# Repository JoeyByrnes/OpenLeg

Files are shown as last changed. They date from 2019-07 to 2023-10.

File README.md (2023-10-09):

<p align="center">
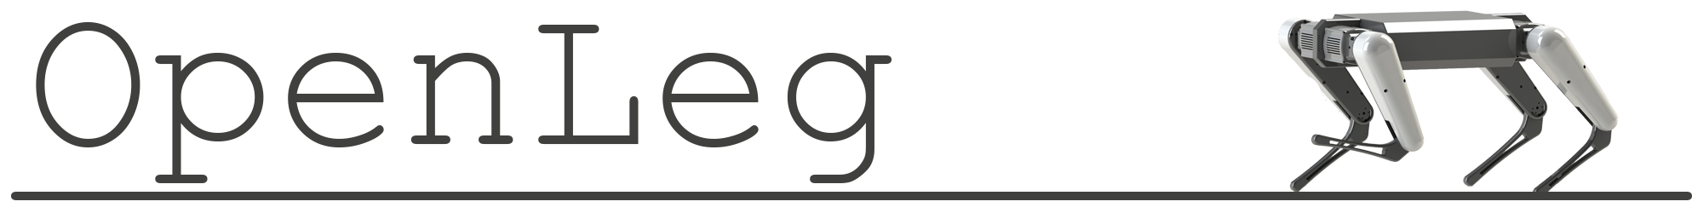
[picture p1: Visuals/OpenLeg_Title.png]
  
</p>

OpenLeg started as my Senior Design project for ECE445 at UIUC. The goal of the project is to provide a fully open source robotic leg capable of fast dynamic movements for research and development of quadrupedal robots. OpenLeg is intended to make development of robotic legs and associated algorithms accessible to hobbyists and researchers with tight schedules or budgets. 

All files required for replicating OpenLeg V1 are provided along with an assembly guide. All crucial mechanical and electrical assembly is now documented in the assembly guide. 

Feel free to reach out to me at openlegproject@gmail.com if you are interested in building the leg or contributing to the project.

Please keep in mind- OpenLeg isn't a finished product, it's still very much under development. You can expect everything in the assembly guide to be ready to use but for things not listed in the guide you should expect that there is still development needed to be done.

You can find the OpenLeg V1 Senior Design demo video here: https://www.youtube.com/watch?v=aXOSeKpADnk

Access the Full SolidWorks souce files for OpenLeg V1 in Hardware > OpenLeg_Assembly_Pack_and_Go.zip

OpenLeg has also been featured on the following sites: 
<a href="https://hackaday.com/2019/09/21/openleg-the-open-source-robot-leg/" target="_blank">Hackaday</a> &nbsp;&bull;&nbsp;
<a href="https://www.hackster.io/news/you-can-design-your-own-sophisticated-walking-robot-thanks-to-this-student-project-7c02dde19ade" target="_blank">Hackster</a>&nbsp;&bull;&nbsp;
<a href="https://www.inceptivemind.com/openleg-open-source-project-building-robot-legs/9271/" target="_blank">InceptiveMind</a>&nbsp;&bull;&nbsp;
<a href="https://asgardia.space/en/news/You-Can-Design-Your-Own-Four-Legged-Robot-Without-Designing-Its-Legs-Now" target="_blank">Asgardia</a>

<p align="center">
  
</p>

You can find the OpenLeg V2 Actuator source files in Hardware > OpenLeg_V2_Actuator_Pack_and_Go.zip > Actuator_V1.SLDASM

OpenLeg V2 is no longer just a standalone 2 DOF leg, it's a full 3 DOF leg optimized for use in the OpenLeg Quadruped. 

OpenLeg V2 is based on a modular actuator with a 50Kv motor, planetary gearbox, and FOC controller all built into one unit. This actuator is used for both of the hip joints, while the knee uses a belt transmission for keeping a nice form factor. The belt transmission has however been updated to have far lower friction that the 90 degree twist design in OpenLeg V1.

<p align="center">
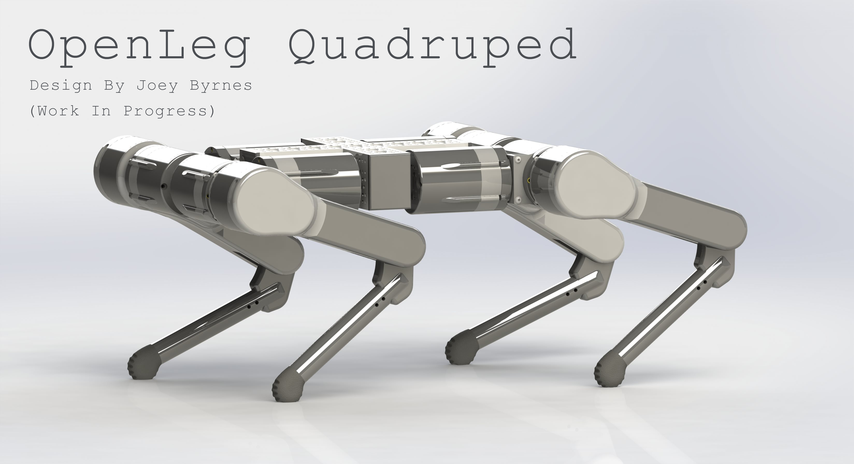
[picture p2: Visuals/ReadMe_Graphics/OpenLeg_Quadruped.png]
  
</p>
<p align="center">
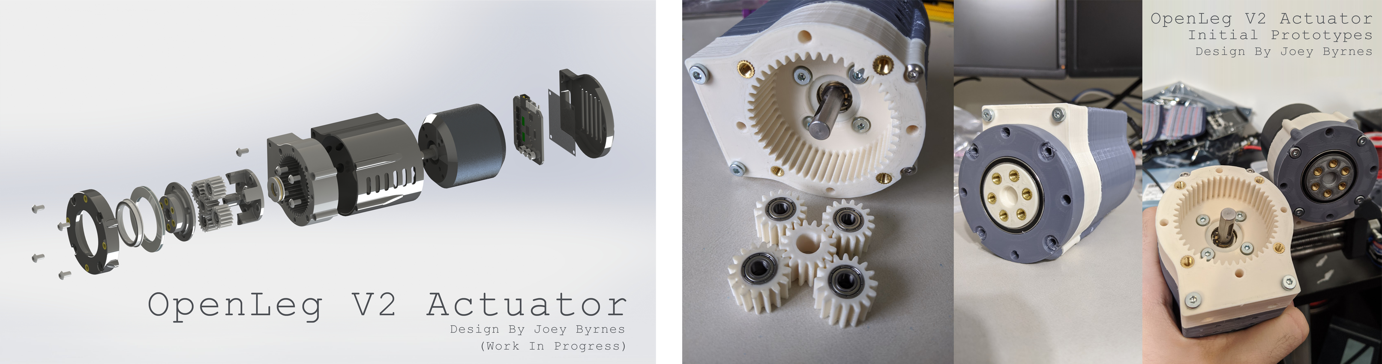
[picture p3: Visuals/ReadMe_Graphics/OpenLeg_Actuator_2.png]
  
</p>

<p align="center">
  
</p>

<p align="center">
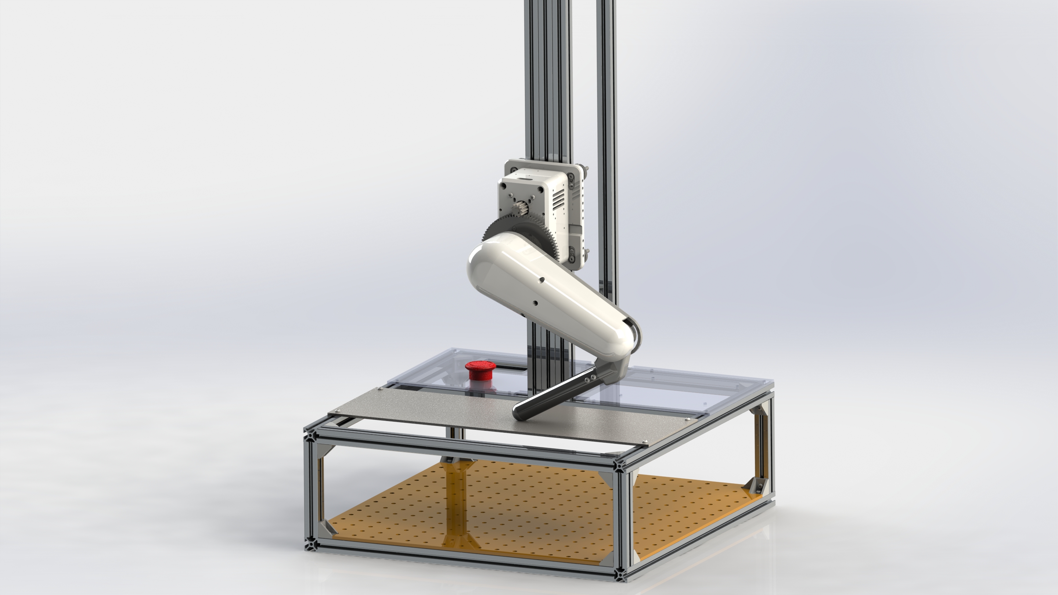
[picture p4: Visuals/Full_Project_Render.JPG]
  
</p>

<p align="center">
  
</p>

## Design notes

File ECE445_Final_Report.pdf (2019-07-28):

# Dynamic Robotic Leg

By

Joseph Byrnes

Kanyon Edvall

Ahsan Qureshi

Final Report for ECE 445, Senior Design, Spring 2019

TA: David Hanley

1 May 2019

Project No. 1

## Abstract

In this project we designed, built, and tested a robotic leg mounted on a development stand. The leg and stand system has three degrees of freedom with two actuated joints in the leg and one degree of freedom provided by a linear rail on the test stand which the leg is mounted to. The leg uses high torque, low cost, consumer-off-the-shelf brushless DC motors. The leg is comprised mostly of custom 3D printed parts and open source electronics. The leg is able to execute trajectories for walking gaits and jumping through an inverse kinematics controller using PID position control. The development stand powers the leg using two modified server grade power supplies and allows for safe testing through multiple emergency-stop buttons and a circuit breaker. We have also created a simulation for trajectories to be developed with and tested in before implementing them on the physical leg.

## Contents

1. Introduction | 4
1.1 Objective | 5
2 Design | 5
2.1 Simulation | 6
2.2 Power Subsystem | 9
2.2.1 Power Supply | 9
2.2.2 Logic Power Delivery | 9
2.2.3 Motor Power Delivery | 9
2.3 Central Control Subsystem | 9
2.3.1 TI F28335 Digital Signal Processor | 9
2.3.2 TI F28335 Breakout PCB | 9
2.3.3 Height Sensing Encoder | 9
2.4 Motor Control Subsystem | 9
2.4.1 Motor Controller | 9
2.4.2 Motor Encoders | 10
2.4.3 Motors | 10
3. Design Verification | 10
3.1 Power Subsystem Verification | 10
3.1.1 Motor Power Delivery | 10
3.1.2 Logic Power Delivery | 10
3.2 Central Control Verification | 10
3.2.1 Leg Height Sensor | 10
3.2.2 F28335 Breakout PCB | 11
3.3 Motor Control Verification | 11
3.3.1 Motor Controller Board | 11

3.3.2 Motor Encoders | 11
3.3.3 Motors | 11
4. Costs | 13
4.1 Parts | 13
4.2 Labor | 13
5. Conclusion | 14
5.1 Accomplishments | 14
5.2 Ethical considerations and Safety Hazards | 14
5.3 Future work | 15
References | 16
Appendix A Requirement and Verification Table | 17

## 1. Introduction

While wheeled robots excel in flat terrain, they still face challenges with navigating a world created for humans [1]. Similarly, aerial robots suffer from difficulties such as moving through confined spaces and interacting with the environment around them. The problem of navigating multi-level environments, including stairs and unstructured environments such as a floor with debris or uneven terrain, has not been fully solved with ground robots. Although aerial robots have been deployed in these situations, they face many obstacles as listed in page 172 of [2]. Legged robots, such as quadrupeds, are able to successfully navigate a multitude of human-oriented environments without the restrictions imposed by aerial and wheeled vehicles. Specifically, dynamically stable quadrupeds hold a great deal of promise for navigating unstructured environments because of their large workspace, ability to reject disturbances quickly, and the flexibility in movements they can perform. Far more research must be conducted before legged robots will be useful in real world deployment. Currently, there is no existing open source platform which researchers are able to use to develop algorithms for legged robotics.

We have created a two degree of freedom robotic leg stabilized on a test frame in order to demonstrate trajectories used for walking gaits. This project demonstrates the feasibility of inexpensive walking robots through a fully functional leg and test rig that can easily be reproduced with consumer off-the-shelf components and built upon to provide the starting point for a novel quadrupedal robot. We will provide an open-source design including all necessary structural components, a complete bill of materials, and necessary software to control the leg. It is our hope that this project can serve as the base for future research projects expanding on dynamic leg control and its applications by providing a ready-to-build leg that handles all low-level control internally.

### 1.1 Objective

While research labs and companies have been developing dynamic legged robots for years— Boston Dynamics’ Spot mini [3], Unitree’s Laikago [4], Ghost Robotics’ Vision [5], MIT’s Cheetah [6], etc— all of these robots use custom motors and/or proprietary control algorithms which are not conducive to increasing the development of legged robotics. Each of the quadrupeds listed above started as a single leg tested on a stabilized platform before integrating the leg into the entire robot. Currently, when developing a new legged robot it is necessary to develop a custom leg as a starting point much like the examples listed above. With a fully open-source, sub one-thousand dollar dynamic robotic leg and controller, we believe we can accelerate the development of legged robotics by reducing entry barrier both technically and financially to increase involvement in the field.

## 2 Design

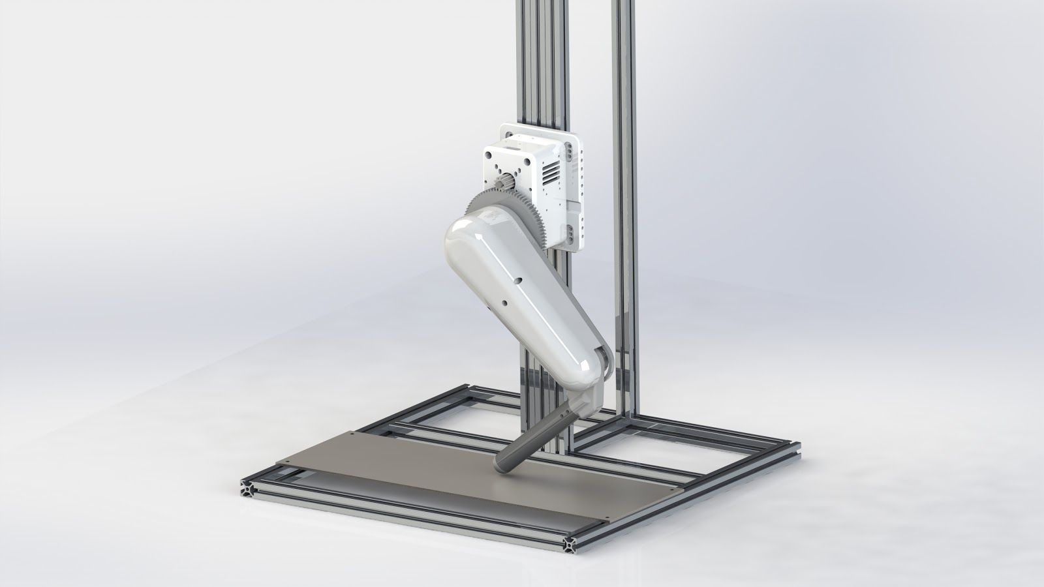
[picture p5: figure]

Figure 1: Full Project 3D Model. Development stands based on stands depicted on page 82 of [7] and page 300 of [8].

The design of the dynamic robotic leg can be divided into three distinct but highly connected categories. First, we designed the mechanical components of the project such as the leg links, ganty, and development stand. Second, we created a mathematical model and simulation for the leg to determine the necessary operating range of the motors. Third, we designed the electrical system based on our expected power and torque requirements.

### 2.1 Simulation

When designing the simulation, we started by creating an inverse kinematic controller for the leg. Since the leg has only two joints, we used a geometric approach to deriving the inverse kinematics equations.

We found that given a coordinate within the leg’s workspace, the joint angles could be calculated using equation 1 and equation 2.

q | − os ( | ) 2 = c

−1
2 * a a 1 * 2

x + y − a − a

2 2
1

2
2
2 | (1)
q | tan2(y, ) | tan2( a | in(q ), | cos(q ) ) 1 = a | x + a | 2 * s | 2 a1 + a2 | 2 | − q2
(2)

Equation 1 and Equation 2 allow us to transform trajectories created in cartesian space into the configuration space of the leg, where q1 and q2 are the hip and knee joint angles respectively, a1 and a2 are the upper leg and lower leg link lengths respectively, and x and y are the coordinate of the foot with respect to the body frame of the leg.

After deriving the inverse kinematics equations, we created a script in MATLAB that generated trajectories in the configuration space of the leg based on desired (x,y) coordinates of the foot over time. We then created a Simulink model shown in Figure 2 which uses Simscape multibody to simulate the physics of the leg. The simulation contains PID position controllers for each joint and allows the user to input a trajectory and plot the required torque at each timestep for executing the trajectory.

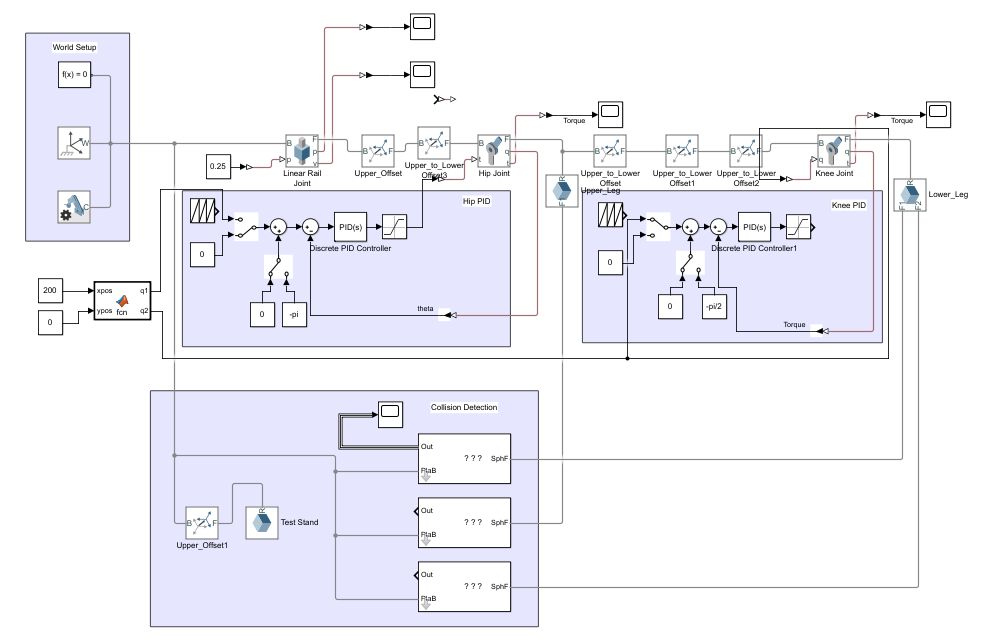
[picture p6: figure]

Figure 2: Simulink Block Diagram using Simscape Multi-Body. Simulates the full system with inverse kinematics controller using independent joint PID position control. Allows plotting of joint torque and position data

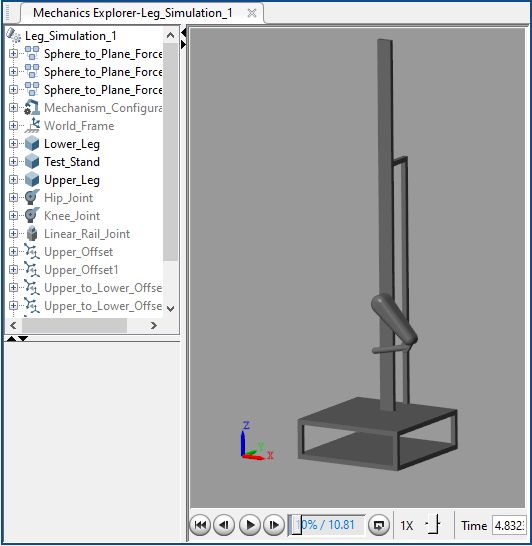
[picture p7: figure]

Figure 3: Physical model of the simulation generated by SimScape Multibody. Manipulations to SIMULINK block diagram update while simulation is running allowing for efficient development of trajectories and live tuning of controller gains

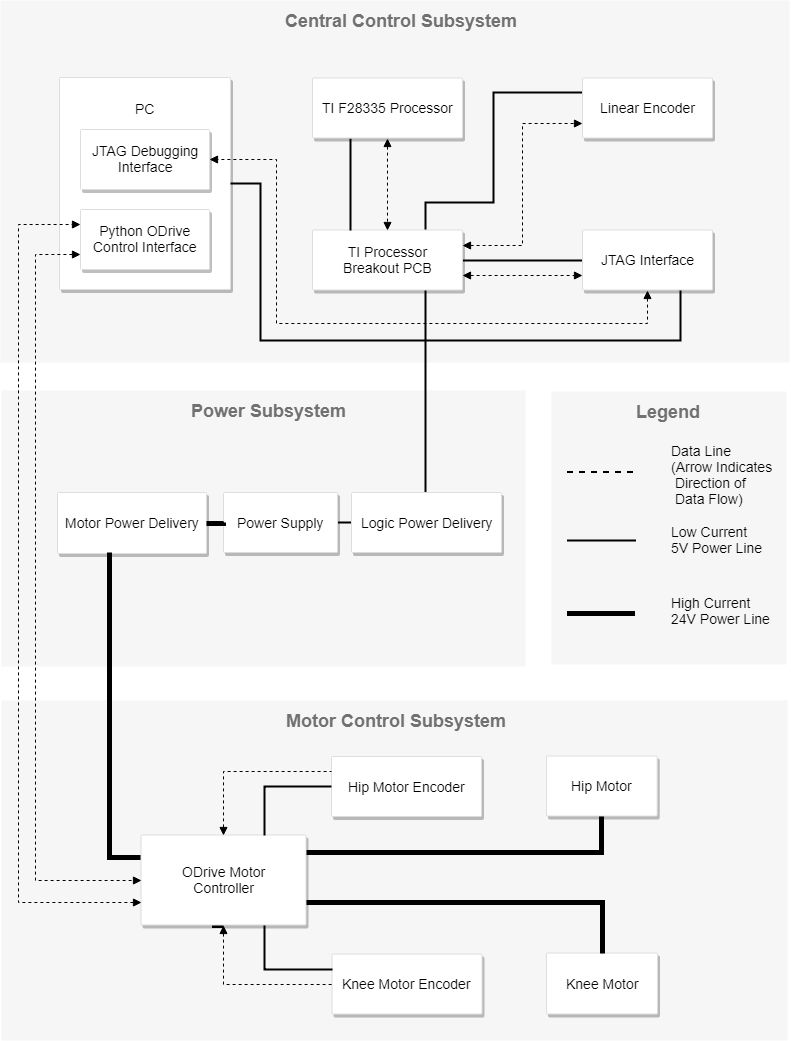
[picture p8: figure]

Figure 4: Full System Block Diagram

### 2.2 Power Subsystem

The power subsystem consists of three modular components, the power supplies, the logic power delivery, and the motor power delivery. These three components work together to reliably meet the high power demands of our project.

### 2.2.1 Power Supply

Two 12 volt, 750 watt server grade power supplies are connected in series to provide a maximum of 1500 watts at 24 volts. A relay board controls the power supply’s operation for safety and ease-of-use.

### 2.2.2 Logic Power Delivery

The logic power delivery system consists of a wiring harness to connect the power supply to the Processor Breakout PCB as well as a 5 V switching regulator on the PCB to power the TI DSP.

### 2.2.3 Motor Power Delivery

The motor power delivery system consists of a wiring harness to connect the power supply to each motor controller board as well as a 60 A circuit breaker to provide overcurrent protection.

### 2.3 Central Control Subsystem

### 2.3.1 TI F28335 Digital Signal Processor

We use the TMS320F28335 controlCARD to record the height of our leg through the hardware quadrature encoder input.

### 2.3.2 TI F28335 Breakout PCB

The Breakout PCB provides connections to all necessary GPIO on the ControlCARD and provides power regulation and protection to the processor. The board provides a 20-pin JTAG connection for programming and real time debugging.

### 2.3.3 Height Sensing Encoder

We use an incremental encoder to measure the movement of a belt loop attached to the gantry to track the height of the leg. The encoder has a resolution of 2000 CPR, and reads the orientation of a magnet mounted on a 20 tooth pulley, spun by a 2 mm pitch timing belt. This results in a sensing precision of 0.02 mm.

### 2.4 Motor Control Subsystem

### 2.4.1 Motor Controller

Each motor is driven by an ODrive motor controller. The ODrive controls the position, velocity, and torque of each motor.

### 2.4.2 Motor Encoders

We use absolute magnetic encoders with a precision of 2000 CPR to measure the rotation of the motors. The encoders connect directly to the ODrive for providing feedback for the PID position controller as well as rotor position data for the Field-Oriented-Control algorithm.

### 2.4.3 Motors

Motor selection was integral to the success of our project. We selected two 6354 brushless DC (BLDC) motors. These motors were selected for their high torque capabilities, 0.16 Nm/A, and large current rating of 2450 W.

## 3. Design Verification

The verification of our project was ultimately a full-system test of the dynamic leg including tasks such as trajectory following and jumping. To ensure our project was fully functional when completed, we made use of modular design and unit testing, verifying each component individually before integrating it into the larger system.

### 3.1 Power Subsystem Verification

### 3.1.1 Motor Power Delivery

While modifying the power supplies to output between 23.7 V and 24.7 V when connected in series, we used a multimeter to ensure that the output voltage of each power supply individually was outputting the required voltage. After finding that the voltage of each power supply was different, we used the internal voltage adjustment potentiometer to adjust the output voltages to each be exactly half of our desired output voltage. We found that the cooling fan running at full speed dropped the output voltage of the supplies by 0.03 V. We accounted for this drop during adjustment as well as anticipated voltage drops due to the high current pulled by the joint motors by setting the output voltage to 24.4 V.

### 3.1.2 Logic Power Delivery

After connecting the F28335 Breakout PCB to the power supplies, we tested the voltage output of the on-board switching voltage regulator. We found that the voltage remained steady at 5.26 V, which is in our required operating range.

### 3.2 Central Control Verification

### 3.2.1 Leg Height Sensor

Verification of the leg high sensor was sufficiently complex. We designed a belt system anchored to the gantry with a pulley on the top and bottom of the development stand. When the leg moves, the anchored belt rotates the pulleys. A magnetic encoder can then read the rotation and angle of the shaft on the lower pulley, thus giving the height of the leg at any given time. The challenge of this verification was, given the high pulse count of the encoder, normal encoder polling techniques failed to capture a number of pulses when the leg moved quickly (i.e. jumping). To remedy this, we used the hardware quadrature encoder reading implementation embedded in the TMS320F28335 controlCARD. This allowed us to read the encoder’s impulses entirely using hardware and thus was fast enough to keep up with the exceptionally high pulse rate. We verified our accuracy by moving the gantry up or down a known, measured amount, and checking the resulting encoder output to ensure it was accurate.

### 3.2.2 F28335 Breakout PCB

The F28335 Breakout PCB was designed to provide convenient, low cost connection to the F28335 ControlCARD. As previously mentioned, we verified the voltage provided by the on-board regulators. The steady 5.26 V output was within our design tolerances. Additionally, we verified the JTAG breakout worked as intended, allowing us to use the SEGGER J-LINK as a JTAG interface between the ControlCARD and our computer.

### 3.3 Motor Control Verification

### 3.3.1 Motor Controller Board

One key aspect of the motor controllers we selected was its ability to output 35 A continuous current. We set up our motors to pull 35A continuous current and verified that the controller functioned as intended, while remaining under 50 °C.

### 3.3.2 Motor Encoders

In order to get accurate, closed loop positional feedback, we needed to verify the accuracy and reliability of our encoders. We rotated the motor’s shaft a known angle and compared this against the angle reported by the encoder. The resulting difference was within our tolerance of 0.25 degrees of the true angle.

### 3.3.3 Motors

The final aspect of our motor control was the motors themselves. To verify our motors would function reliably, we ran 30 A continuously through them, ensuring the motors remained below 65 °C. We also verified the motor’s torque output, first in the datasheet, and then using a luggage scale to read the force it could apply.

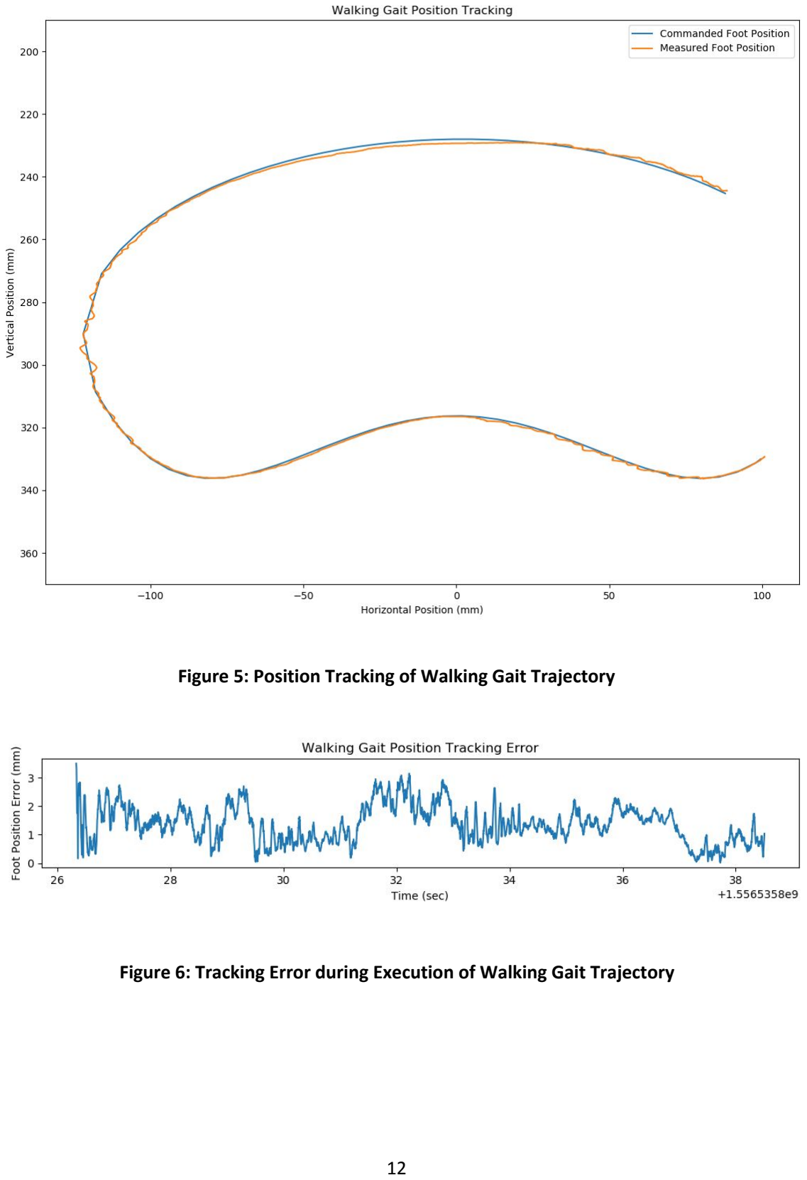
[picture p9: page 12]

Figure 5: Position Tracking of Walking Gait Trajectory

Figure 6: Tracking Error during Execution of Walking Gait Trajectory

## 4. Costs

### 4.1 Parts

Table 1: Project Cost

Part Name | Description | Manufacturer/Supplier | Quantity | Unit Cost | Total Cost
TMDSCNCD28335 | F28335 ControlCard | Texas Instruments | 1 | $69.00 | $69.00
ODrive | Motor Controller | ODrive Robotics | 1 | $119.00 | $119.00
6354 60KV Motor | Brushless Motor | E-Power Hobby | 2 | $90.00 | $180.00
AS5047D | Magnetic Encoder | DigiKey | 3 | $16.76 | $50.28
Central PCB | Regulator/data routing PCB | PCBWay | 1 | $5.00 | $5.00
3D Printer Filament | PLA Filament | Hatchbox | 2 | $24.00 | $48.00
Knee Axle | 1/2 Inch Hex Shaft | Vex | 1 | $11.99 | $11.99
Bearings | 1/2 Inch Hex bearing | Vex | 6 | $2.99 | $17.94
Motor Mounting Screws | M4x12 Screws | Amazon | 1 | $3.99 | $3.99
T-Slot Extrusion | 10 x 1m T-slot 2020 | ZYLTech | 1 | $49.99 | $49.99
T-Slot Angle Brackets | 12 x Angle brackets | ZYLTech | 2 | $6.95 | $13.90
Power Supply | 2x 12v 750w Server Power supply | Dell / Ebay | 1 | $27.99 | $27.99
T-Slot wheels | 10 x T-slot wheels for gantry | Amazon | 1 | $7.99 | $7.99
SEGGER J-LINK | JTAG Debugger | Segger / Mouser | 1 | $60 | $60.00
| | | Total Robot Cost: | | $665.07

### 4.2 Labor

Table 2: Labor Cost

Team Member: | Hourly Wage | Weekly Hours | Number of weeks | Multiplier | Cost per Member
Joseph Byrnes | $35.00 | 30 | 12 | 2.5 | $31,500.00
Ahsan Qureshi | $35.00 | 12 | 12 | 2.5 | $12,600.00
Kanyon Edvall | $35.00 | 12 | 12 | 2.5 | $12,600.00
| | | | Total Labor Cost: | $56,700.00

## 5. Conclusion

### 5.1 Accomplishments

Our project exceeded expectations in terms of accuracy and jumping height. The leg is capable of jumping over 20 cm. We successfully implemented an inverse kinematic controller based on independent joint PID position controllers. The controllers allow the leg to execute various movement trajectories such as walking and running gaits, while staying within 3.5 mm of the target end effector positions. We were able to accomplish these goals while only using 3D printed parts and off-the-shelf components.

### 5.2 Ethical considerations and Safety Hazards

Within our project, there are several potential safety hazards.The first concern that we will deal with is disabling the robot leg if it begins to move unexpectedly. To mitigate this issue we included emergency stop buttons which disable power to the motors. Additionally, our motor controllers have a failsafe enabled that disables the motors if no communication is received after a predetermined number of missed packets or time. Another safety hazard that we considered is the inclusion of high wattage power supply units within our design. Continuously drawing a high amperage may overload lab circuit breakers and power supply connections can be hazardous if not enclosed properly. We included a power dissipation resistor to prevent the regenerative current of the motor from damaging the overall electrical system of the robot or power supply units. Additionally, we added 3D print protective enclosures to ensure all exposed connections were properly covered.

A robotic leg by itself does not prove to have ethical challenges, however, once the leg is applied to a mobile platform, it may present ethical challenges. Isaac Asimov founded the idea of robots and established the Three Laws of Robotics, being 1) A robot may not injure a human being or, through inaction, allow a human being to come to harm; 2) A robot must obey the orders given it by human beings, except where such orders would conflict with the First Law; and 3) A robot must protect its own existence as long as such protection does not conflict with the First or Second Laws [09]. An autonomous mobile platform could be designed using our legs which could be used as a mount for a weapon, or as a vehicle to perform illegal surveillance. These acts would violate the IEEE code of ethics, specifically, code 1 and code 9 [10]. We would prevent our designs from being used for harmful purposes by withholding our leg and technology associated with it from the public sphere. We would vet potential consumers of our product so that we can prevent it being used for purposes we find to be in violation of our ethics. At the same time, our research could be used for positives as well. For example, having met with officers of the UIPD, we have discussed future applications of our robotic leg such as the integration of the leg onto a mobile reconnaissance platform. This platform would provide increased safety to the officers by distancing them from potential threats such as explosive devices or hidden suspects.

### 5.3 Future work

Currently, we have implemented a position based controller, but we plan to develop a dynamic task space controller because it provides increased control and superior tracking when executing trajectories. We will be releasing our entire project as an open source platform for legged robotics research and education. We will be continuing to develop the JoeDrive BLDC motor controller and releasing it as an open source addition to the ODrive project. We also envision that the leg could be incorporated into a platform with multiple legs in future work by ourselves or users of the open source project.

## References

[1] Chakraborty, N. and Ghosal, A. (2019). Kinematics of wheeled mobile robots on uneven terrain. [online] Science Direct. Available at: https://www.sciencedirect.com/science/article/pii/S0094114X04001478 [Accessed 22 Feb. 2019]
[2] G. Chowdhary, F. Dellaert, M. Kaess, E. Johnson and A. Wu, "Autonomous Flight in GPS-Denied Environments Using Monocular Vision and Inertial Sensors", Arc.aiaa.org, 2013. [Online]. Available: https://arc.aiaa.org/doi/abs/10.2514/1.I010023. [Accessed: 22- Feb- 2019].
[3] Bostondynamics.com. (2019). SpotMini | Good things Come In Small Packages. [online] Available at:
https://www.bostondynamics.com/spot-mini [Accessed 22 Feb. 2019].
[4] Unitree.cc. (2019). Unitree-Laikago. [online] Available at: http://www.unitree.cc/e/action/ShowInfo.php?classid=6&id=1 [Accessed 22 Feb. 2019].
[5] Revolutionizing Legged Robots | Ghost. (2019). Legged UGVs | Ghost Robotics. [online] Available at:
https://www.ghostrobotics.io/robots [Accessed 22 Feb. 2019].
[6] Chu, J. (2019). “Blind” Cheetah 3 robot can climb stairs littered with obstacles. [online] MIT News. Available at: http://news.mit.edu/2018/blind-cheetah-robot-climb-stairs-obstacles-disaster-zones-0705 [Accessed 22 Feb. 2019].
[7] Kalouche, S. (2019). Design for 3D Agility and Virtual Compliance using Proprioceptive Force Control in Dynamic Legged Robots. [online] Ri.cmu.edu. Available at: https://www.ri.cmu.edu/pub_files/2016/8/kaloucheThesis.pdf [Accessed 22 Feb. 2019].
[8] Ding, Y. and Park, H. (2019). Design and experimental implementation of a quasi-direct-drive leg for optimized jumping - IEEE Conference Publication. [online] Ieeexplore.ieee.org. Available at: https://ieeexplore.ieee.org/stamp/stamp.jsp?tp=&arnumber=8202172 [Accessed 22 Feb. 2019].
[9] B. Deng, “Machine ethics: The robot's dilemma,” Nature News, 01-Jul-2015. [Online]. Available: https://www.nature.com/news/machine-ethics-the-robot-s-dilemma-1.17881. [Accessed: 22-Feb-2019].
[10] ieee.org. (2019). IEEE Code of Ethics. [online] Available at: http://www.ieee.org/about/corporate/governance/p7-8.html [Accessed 22 Feb. 2019].

Appendix A | Requirement and Verification Table
Requirement | Verification

Power Supplies

Provided voltage must stay between 23.7V and 24.7V | Use a multimeter to confirm that the output of the power supply stays within 23.7V and 24.7V during 30A operation of each motor.
Must provide a minimum of 15A continuous current per motor. At 24V, this corresponds to a maximum power output of 1500W | Set both motors to draw 15A continuously and confirm with a current probe that at least 30A is being supplied to each motor.

Motor Power Delivery

Use wire that does not cause a voltage drop of more than 1.5% of the power supply voltage.

Measure voltage drop across the power cables using a multimeter and confirm that drop is below 1.5% of power supply voltage.

Logic Power Delivery

Use wire that does not cause a voltage drop of more than 1.5% of the power supply voltage.

Measure voltage drop across the power cables using a multimeter and confirm that drop is below 1.5% of power supply voltage.

Central Control Processor

Must be able to perform all dynamics calculations for our controller in less than 1 millisecond.

Output a 0v signal through an output of the processor when the calculations are finished and set the signal to 5v when the periodic task starts again. Confirm using an oscilloscope that the processor is not being overloaded by measuring the duty cycle of the signal, confirm duty cycle is under 1ms.

F28335 Breakout PCB

Board must continually supply 4.9 to 5.5 volts to the ControlCARD. | Using a multimeter, read the voltage at the output of the regulators when leg is stationary and when 30A per motor is being supplied to ensure regulators are not affected by voltage sag due to the the motor power system. Verify the voltage reading is between 4.9V and 5.1V.
Regulators must stay below 50°C for at least 30 minutes of operation under room temperature | Using an infrared thermometer, measure the temperature of the regulators after 30 minutes of operation.

Must breakout the ControlCARD’s JTAG interface for programming using an Atmel ICE programmer. | Connect PCB to a computer using Atmel ICE programmer and confirm proper firmware upload and debugging communication by setting a variable in real time through the Code Composer Studio expressions interface. Confirm variable has changed as expected.
Must provide USB access to the ControlCARD’s serial interface. | Connect ControlCard to PuTTy Terminal and confirm debugging data such as joint angle sent through USB Serial port is functioning.

Height Sensing Encoder

Must measure robot height with accuracy of at least 2mm | Using calipers, move the leg up and down by 1mm at a time and record distance travelled reported by the encoder/processor. Readings are considered good if measured distances is within + or - 1mm of manually measured distance.
Must report distance travelled with a frequency of at least 1ms. | Connect encoder to oscilloscope and measure frequency of data output. Ensure period is less than or equal to 1ms.

Motor Controller

Must support current sensing hardware to achieve torque-based control. Current sensing must be accurate to 5% of actual value. | Using an ammeter, measure current draw on motor power lines. Confirm that measured value is within 5% of the motor controller sensed value.
Must support current output control to achieve torque-based control. Current output must be accurate to 5% of set value. | Using a high-precision lab scale confirm that the torque output from the joint is within 5% of the set torque value.
Must deliver a minimum of 30A continuous current for 30 seconds without rising above 50°C. | Use an infrared thermometer to measure the heat being radiated from the MOSFETS in the motor drive circuit, record and plot the data over the period of 60 seconds of continuous operation. Simultaneously, use a non contact multimeter to measure the current provided to make sure it is 30A for the entire operation.

Motor Encoders

Must report angle within 1 degrees of true angle.

Connect the encoder to a stepper motor and rotate the shaft for a known amount of steps for one full rotation. Record the position data from the encoder and confirm that the encoder reports the angle within 1 degree of the true angle throughout the entire rotation.

Must have data output frequency of 1000 Hz or greater to achieve joint angle updates every 1 ms.

Connect encoder with counter interface to an oscilloscope and measure frequency of data output. Ensure period is less than or equal to 1ms.

Motors

Must allow for up to 30A continuous current for 30 seconds without damaging the motor coils or raising the temperature of the plastic enclosure above 65°C. | Using an infrared thermometer, measure the temperature of the enclosure after 10 minutes of operation. Ensure it is below 65°C.
Must have a torque constant of at least 0.05Nm/A. | Using a spring scale or digital luggage scale, confirm that the torque output from the joint is at least 0.05Nm when 1A is applied.
Must be less than or equal to 63mm in diameter and less than or equal to 90mm long to fit in motor housing. | Measure the motor using calipers with a precision of at least 1/10 mm.

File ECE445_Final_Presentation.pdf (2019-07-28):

### Dynamic Robotic Leg

Joseph Byrnes | Kanyon Edvall | Ahsan Qureshi

ECE 445 Senior Design: Team 1

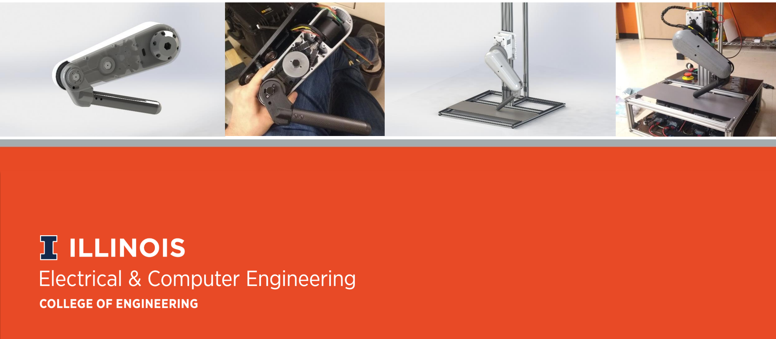
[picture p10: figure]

- Lack of open-source, low cost legged robotics projects

– Long development time for new research

– High cost of development

– High technical barrier for entry

Problem Statement

- Open-Source Robotic Leg & Test Frame

– Research and educational platform

– Three degree of freedom system
- Two actuated joints

– Brushless motors
- High torque & high efficiency

– Comprised of 3D-printed and consumer-off-the-shelf parts

Our Solution

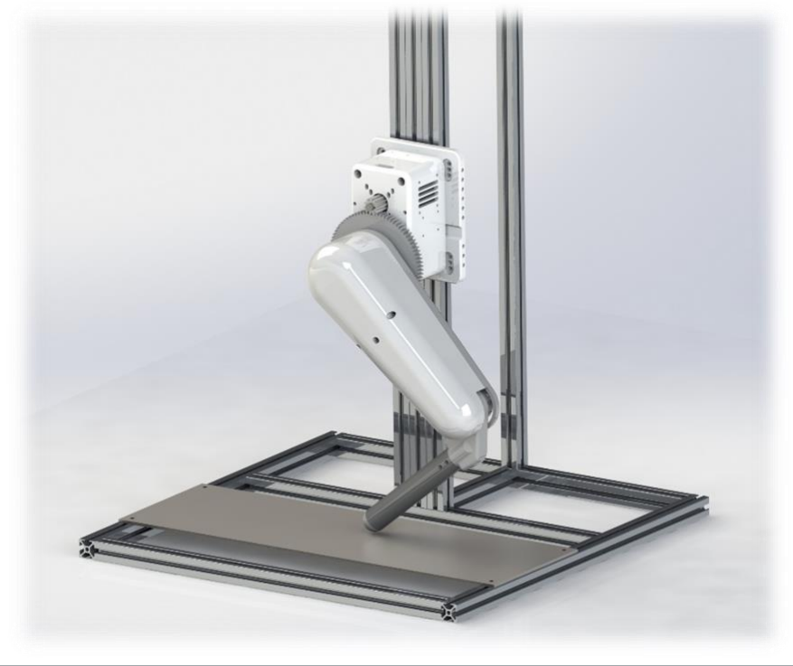
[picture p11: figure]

- Lowers the barrier for legged robotics algorithm development by providing an open source and functionally abstracted robotic leg

Our Solution

Downloadable 3D Printing Files | Open Source Software | Open Source Electronics

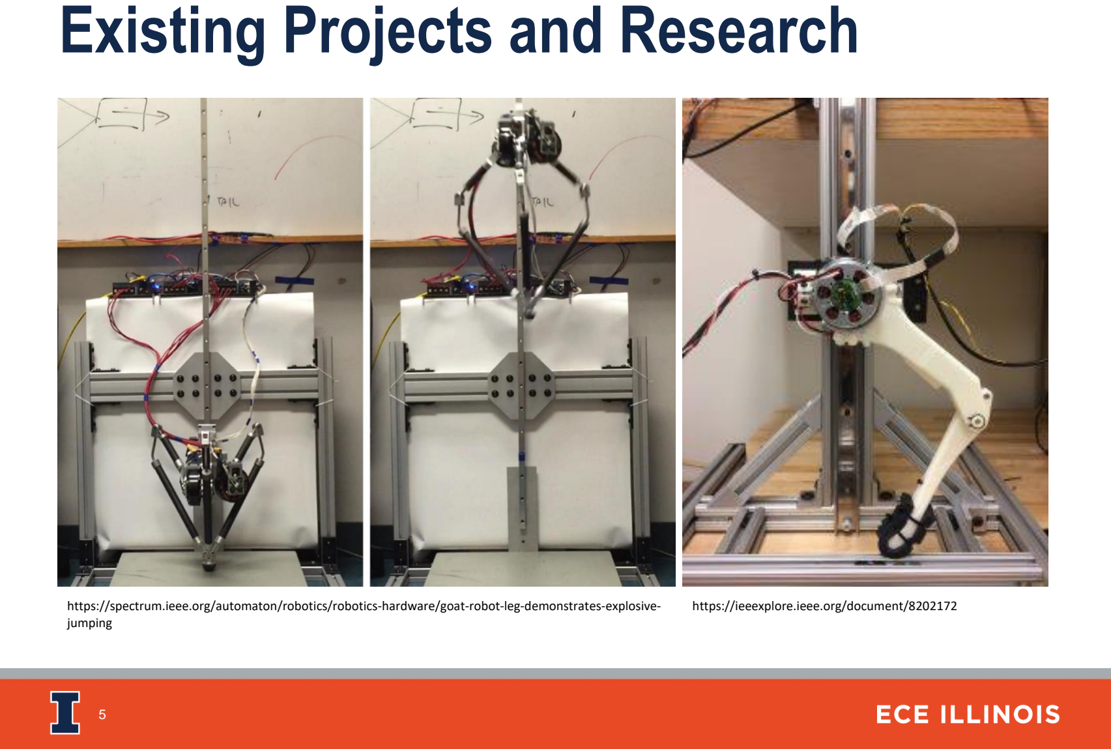
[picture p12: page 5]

Existing Projects and Research

https://spectrum.ieee.org/automaton/robotics/robotics-hardware/goat-robot-leg-demonstrates-explosive-jumping

https://ieeexplore.ieee.org/document/8202172

- Low Cost
- Fully Open-Source
- High Torque Density
- Simple 2 Degree of Freedom actuation

Project Highlights

- Code Shared on GitHub
- Includes a Simulink Block Breakdown of Entire System
- User can edit as needed, adding parts or changing controller as desired

Simulation in MATLAB

Inverse Kinematics

q1 | Hip Motor Angle
q2 | Knee Motor Angle
a1 | Upper Leg Link Length
a2 | Lower Leg Link Length
x | Horizontal Position Set Point
y | Vertical Position Set Point

Simulink Block Diagram

Simulink Block Diagram

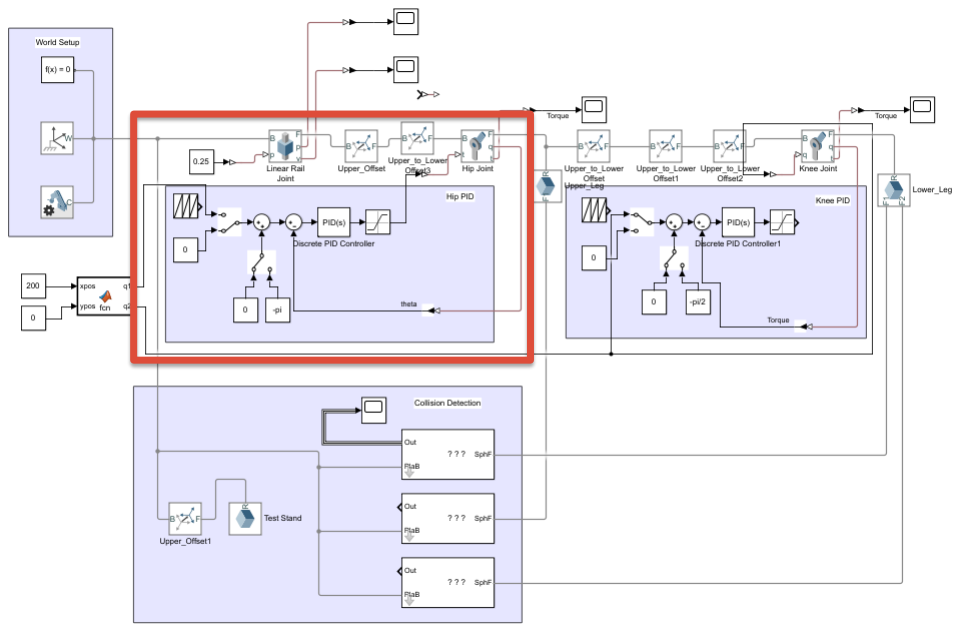
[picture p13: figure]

Hip Joint Controller

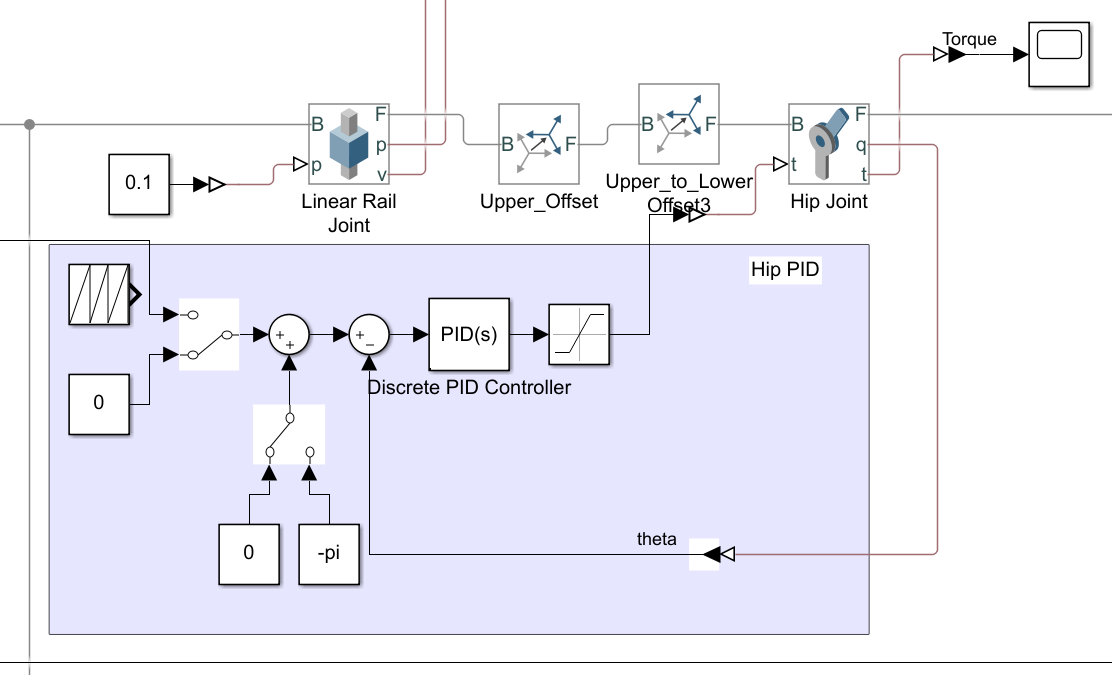
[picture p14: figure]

SimScape Multi-Body Simulation

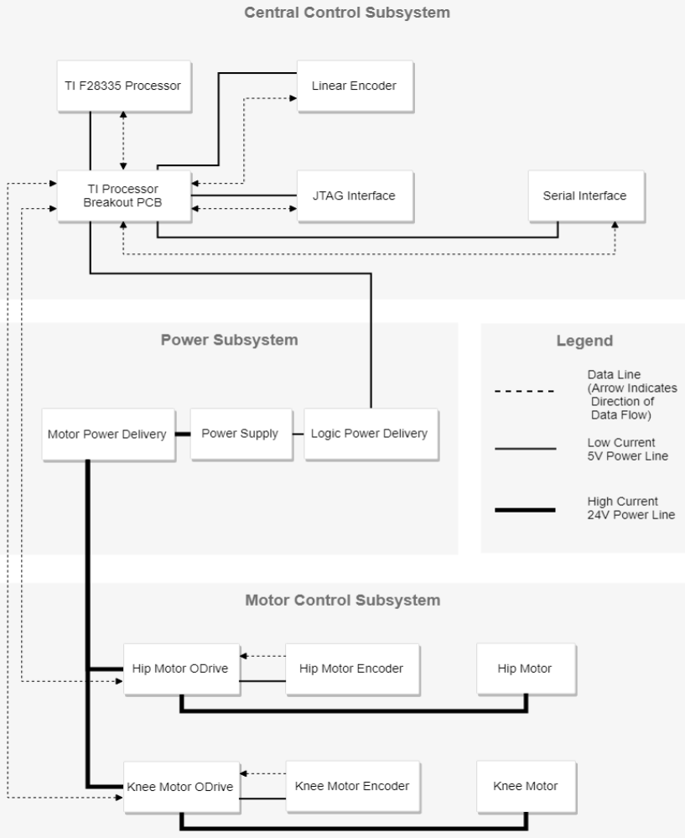
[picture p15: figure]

Design

- Subsystems

– Control Logic & Sensing

– Motor Control

– Power Delivery

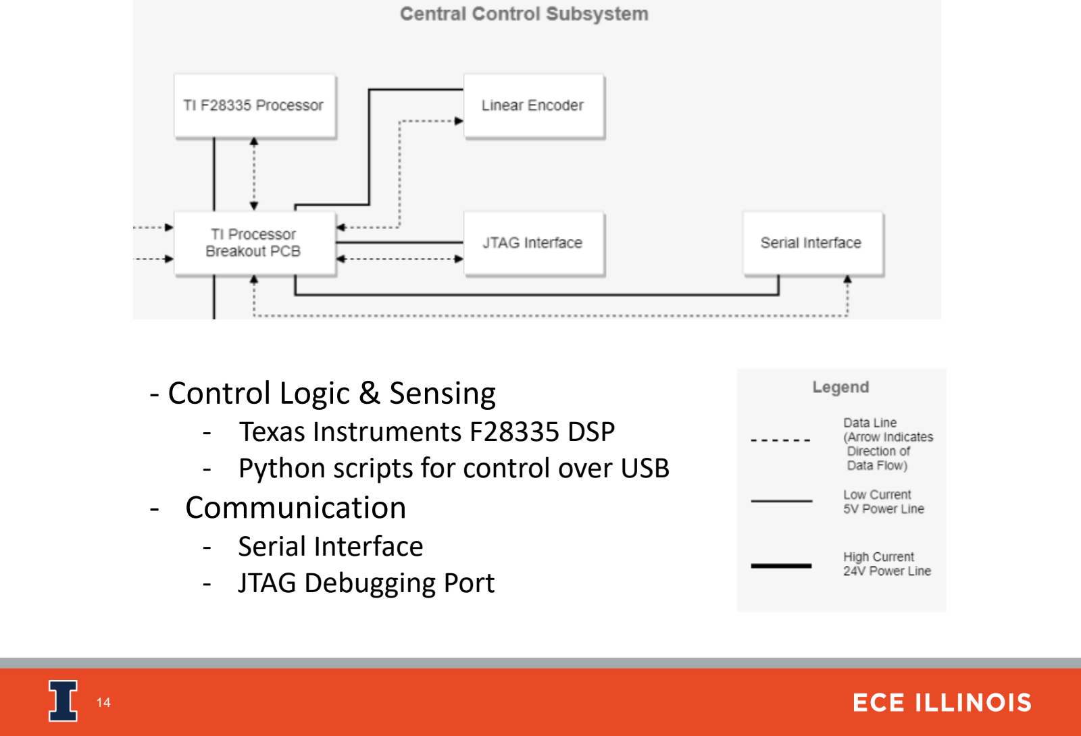
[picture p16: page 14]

- Control Logic & Sensing
- Texas Instruments F28335 DSP
- Python scripts for control over USB
- Communication
- Serial Interface
- JTAG Debugging Port

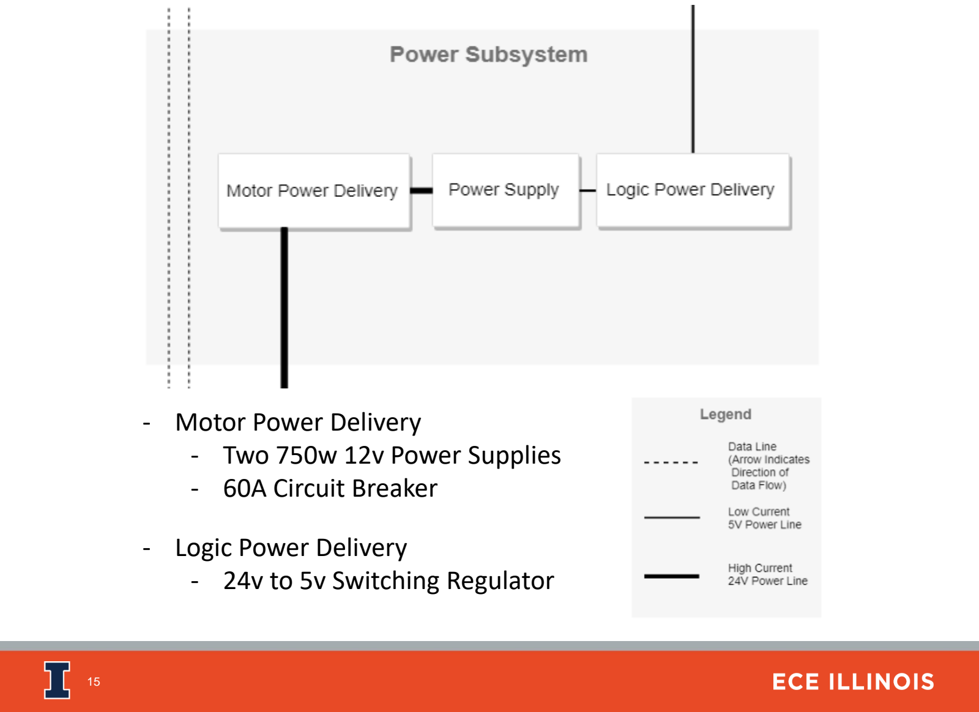
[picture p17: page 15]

- Motor Power Delivery
- Two 750w 12v Power Supplies
- 60A Circuit Breaker
- Logic Power Delivery
- 24v to 5v Switching Regulator

- Motor Control
- 0.16 Nm/A BLDC Motors
- 2000 CPR Magnetic Encoders
- ODrive Motor Controller

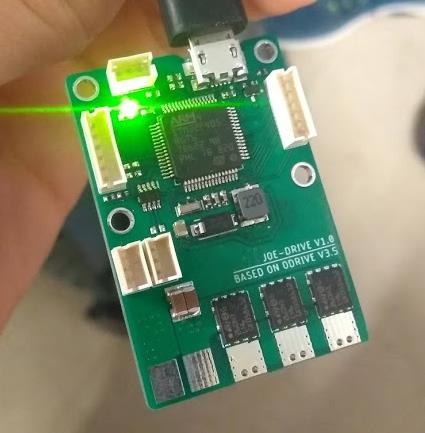
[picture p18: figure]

– Motor Controller Based on ODrive v3.5
– Controls Torque, position, and velocity of single BLDC Motor – 2-layer PCB
– 46 mm tall, 32 mm wide
– Costs under $30 to produce

JoeDrive - Overview

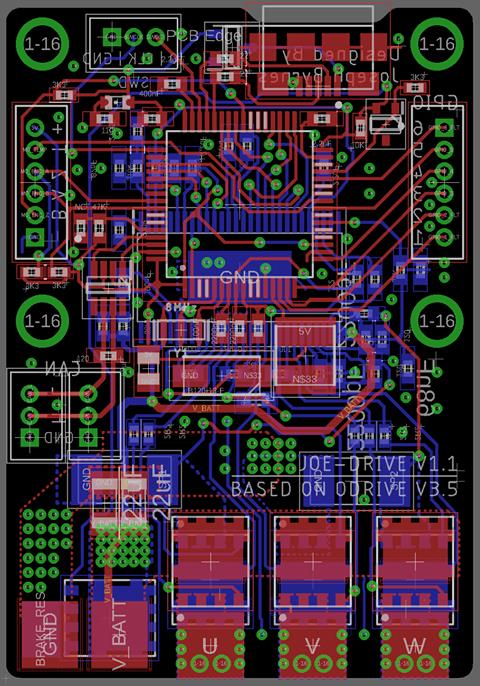
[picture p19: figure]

– Far more compact than
the standard ODrive

– Connections:
- Encoder/Hall Sensors
- Two CAN Ports
- Programming and GPIO
- USB

JoeDrive - Layout

Top | Bottom

Power
Circuit

Logic
Circuit

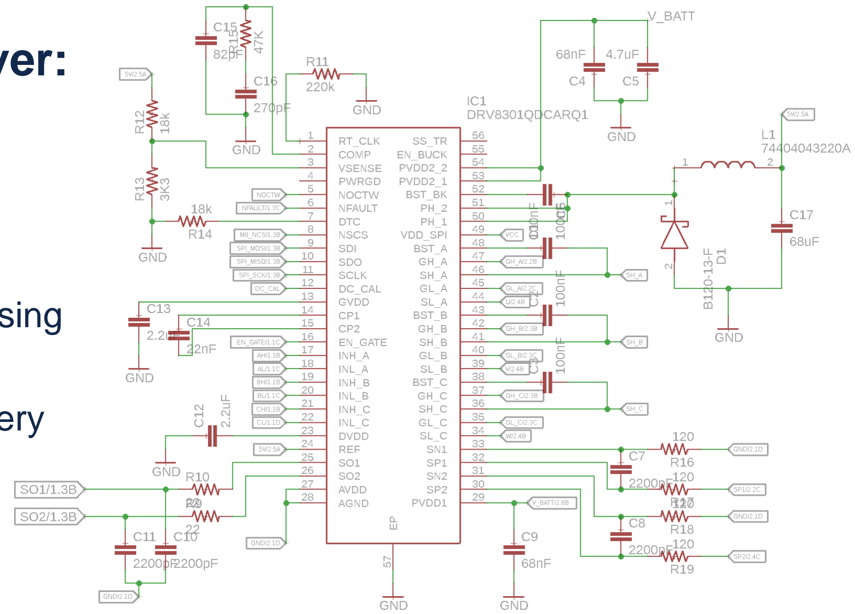
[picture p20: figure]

Gate Driver:

Based on
ODrive v3.5

Current Sensing

Power Delivery
for STM32

JoeDrive - Schematic

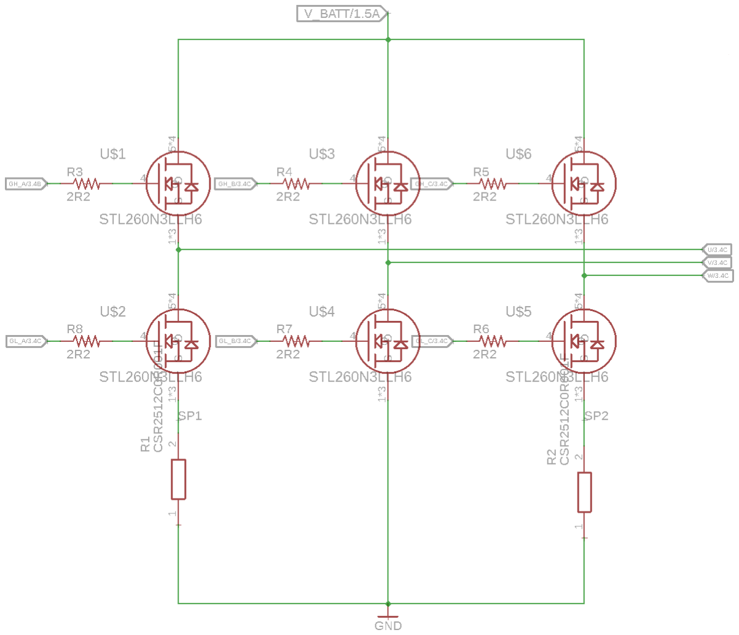
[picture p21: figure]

Power Stage:

– 45 A continuous
current MOSFETs

– Two Shunt
resistors for FOC
and Current
Control

JoeDrive - Schematic

- Hardware Issues

– Brake resistor MOSFET
– DRV 3.3V output
– Current Sensing resistors
– Analog VCC shorted to GND
- Hardware problems fixed in JoeDrive v1.1

JoeDrive - Hardware

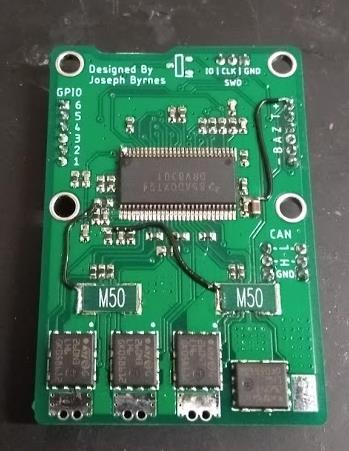
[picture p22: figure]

– Provides conversion from TI 14 pin JTAG to SEGGER 20 pin JTAG debugger port
– Provides connections to necessary GPIO
– Regulates power supply voltage down to 4.9 V to 5.5 V using switching regulator

F28335 DSP Breakout Board

F28335 DSP Breakout Board

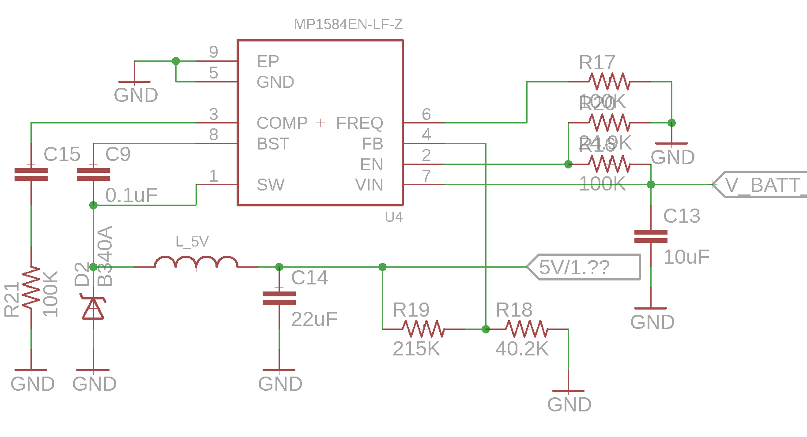
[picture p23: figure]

24 V to 5 V Switching Regulator

– Choosing motors with sufficient torque and power rating was vital to the success of our project

– Important Specifications

- 0.16 Nm/A Torque constant
- 2450 watt power rating
- Diameter of 63 mm, Length of 55 mm
- 3 mm Keyed output shaft
- WYE coil termination
- 558 grams

BLDC Motors

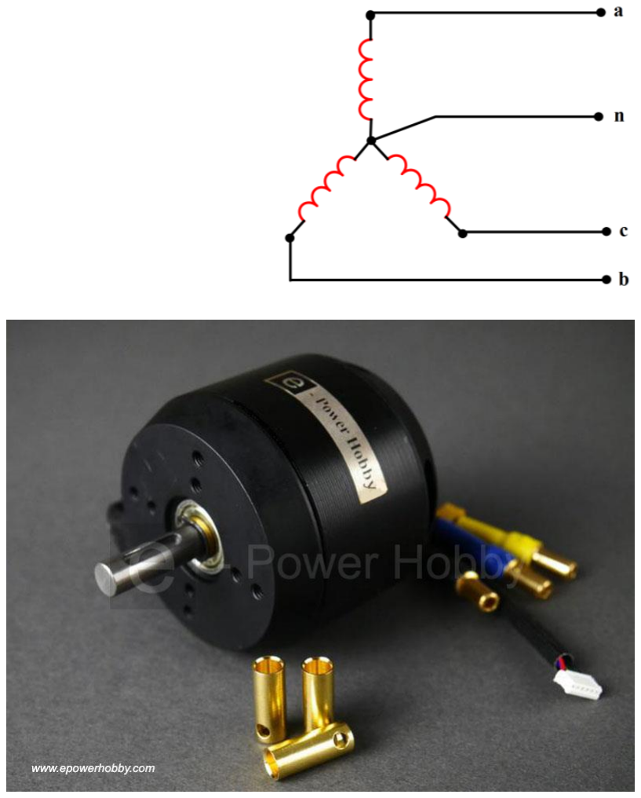
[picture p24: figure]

– AS5047D Magnetic encoders

- small form factor
- low price

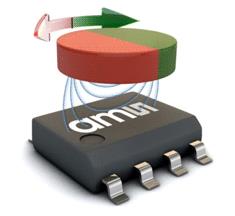
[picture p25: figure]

- Allow for both quadrature and absolute outputs
- Simple installation
- 2000 counts per revolution

Magnetic Encoders

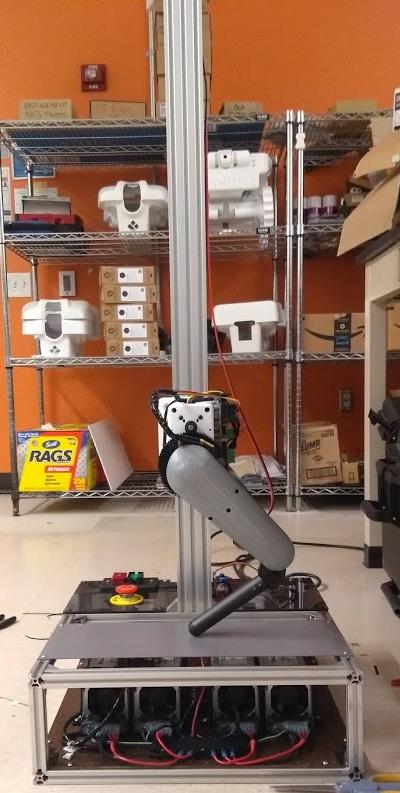
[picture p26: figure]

- Compatible with multiple wall outlet types
- 5 types of safety features including multiple E-Stops, circuit breaker, and switches

Development Stand

- Power Supplies

– Two 12V supplies in series. Produces 1500W at 24V.

– Two PSUs modified for floating ground. Allows boosting to 24V

– Relays control power supply output

Development Stand

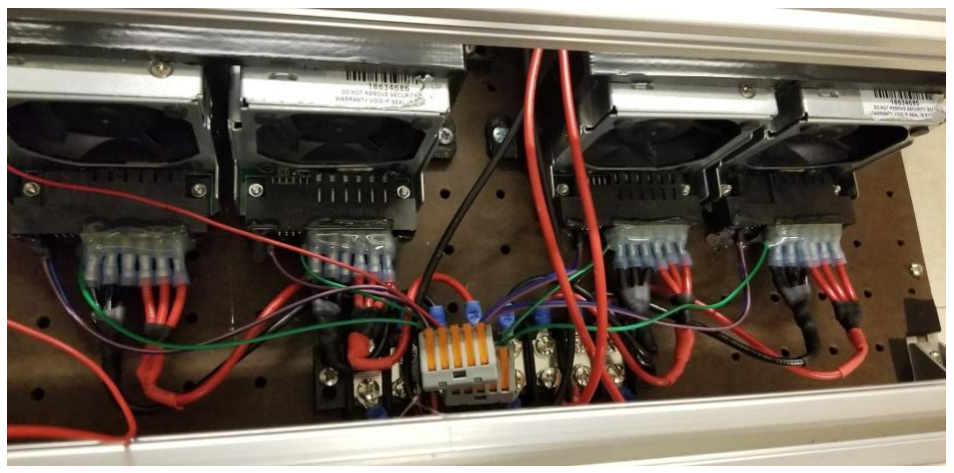
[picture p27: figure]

- PID Tuning

– Position control tracks angle setpoint

– PID tuned for strong disturbance rejection and minimal vibration

– Allows for accurate position tracking

Motor Control

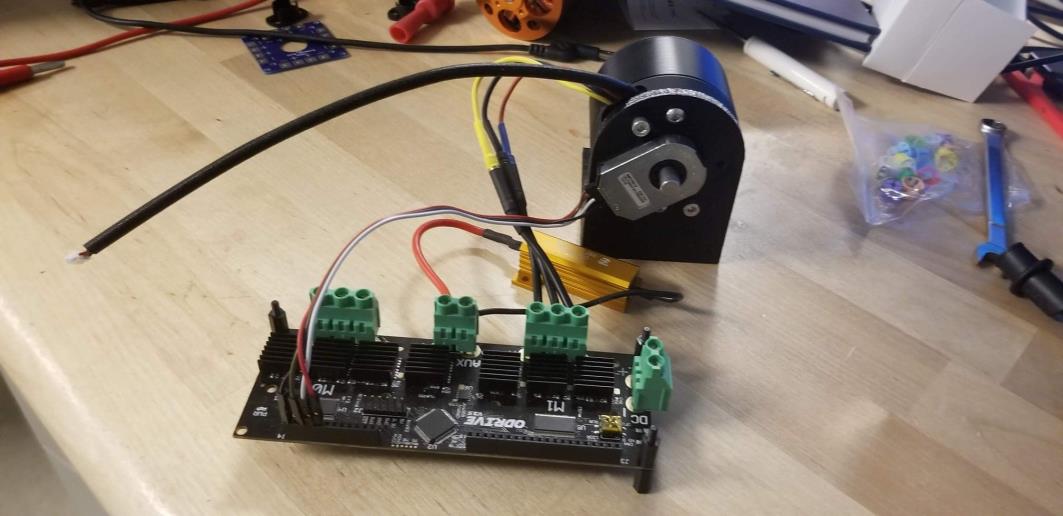
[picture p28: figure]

- Python Interface for ODrive

– Allows for trajectory tracking of predefined paths

– Uses an inverse kinematics controller
– Plots current /
position of motors

– Variety of control
options

ODrive Interface


Trajectory Tracking

Tracking Error During Walking Gait


Foot Position Step Response


Motor Current Usage


- Future work

– Inverse dynamics task space controller
– Open sourcing the project files and creating documentation/tutorials
– Improving the JoeDrive
– Extending development
platform to multiple legs

Conclusion


We would like to extend special thanks to:

- David Hanley
- Chuanzheng (Chad) Li

Acknowledgements

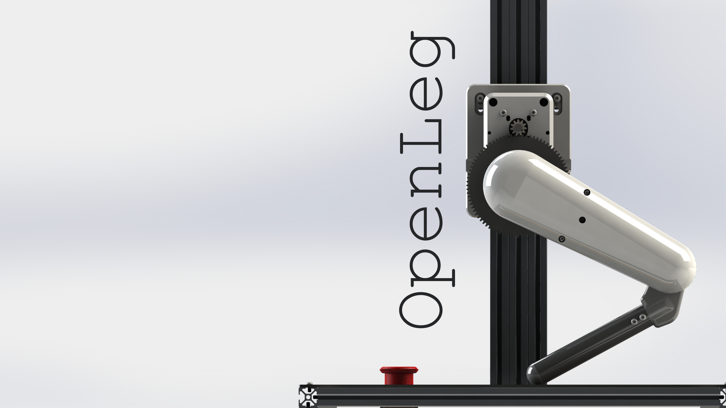
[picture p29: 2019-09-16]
Visuals/OpenLeg_Desktop_BG.png

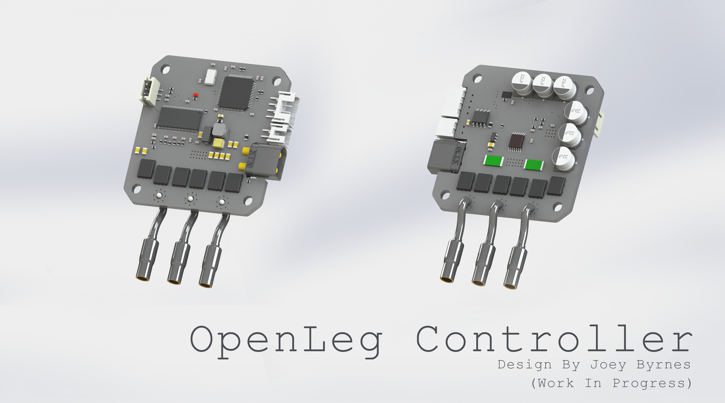
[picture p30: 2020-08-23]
Visuals/ReadMe_Graphics/OpenLeg_Controller.png

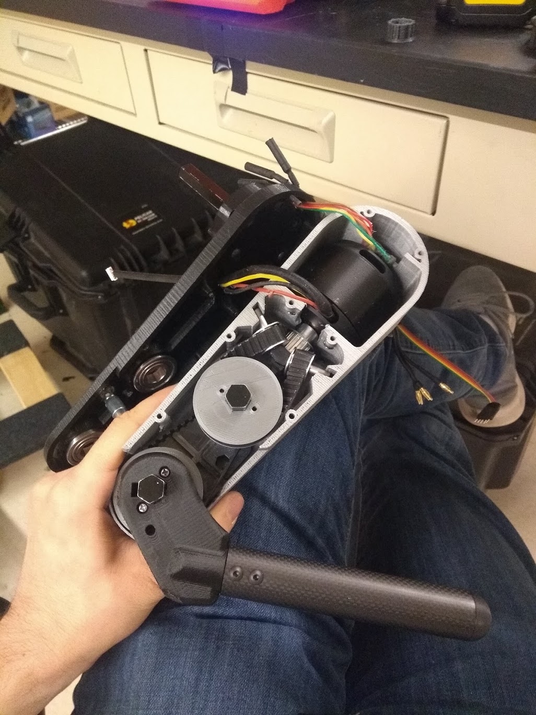
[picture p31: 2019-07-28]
Visuals/4_21_Leg_Internals.jpg

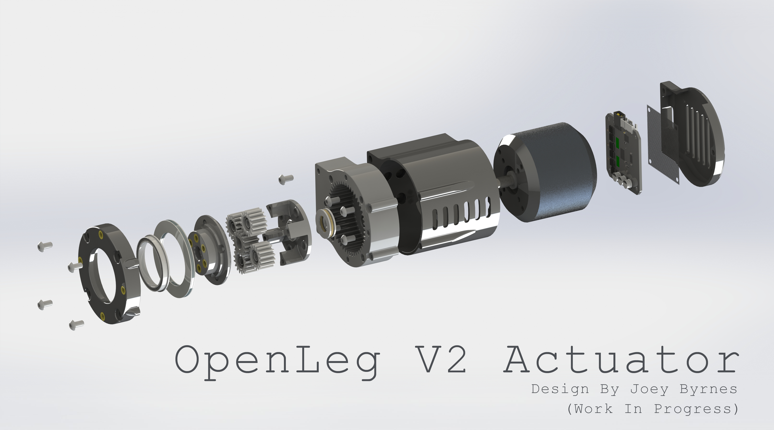
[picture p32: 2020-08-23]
Visuals/ReadMe_Graphics/OpenLeg_Actuator.png

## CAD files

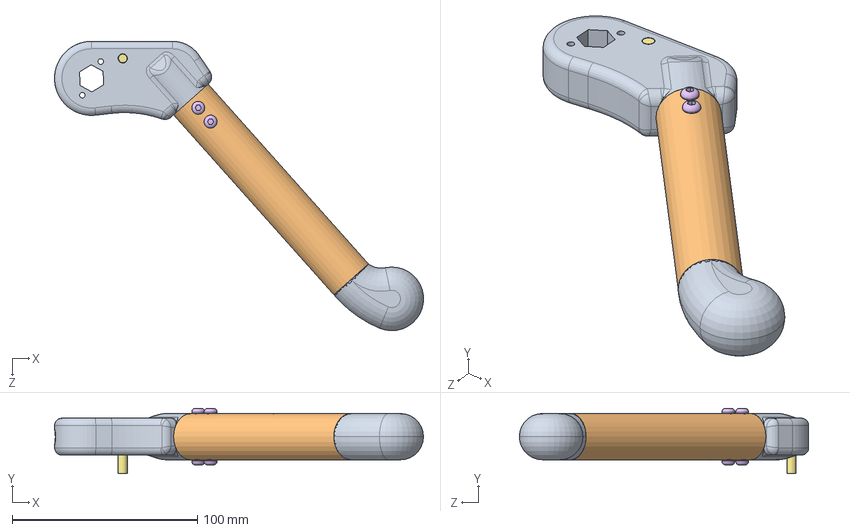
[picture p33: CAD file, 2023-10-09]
Hardware/OpenLeg_Assembly/LowerLegCarbonFiberAsm.SLDASM
199.2 x 35.3 x 156.2 mm
LowerLegCarbonFiberAdapter
LowerLegCarbonFiber
DIN 557 M4_ DIN 557 M4.stp x 6
M4_45mm_Screw_2 x 2
M4_10mm_Screw_2 x 4
Hard_Stop_Shaft
M4_8mm_Screw_2 x 2
Curved_foot

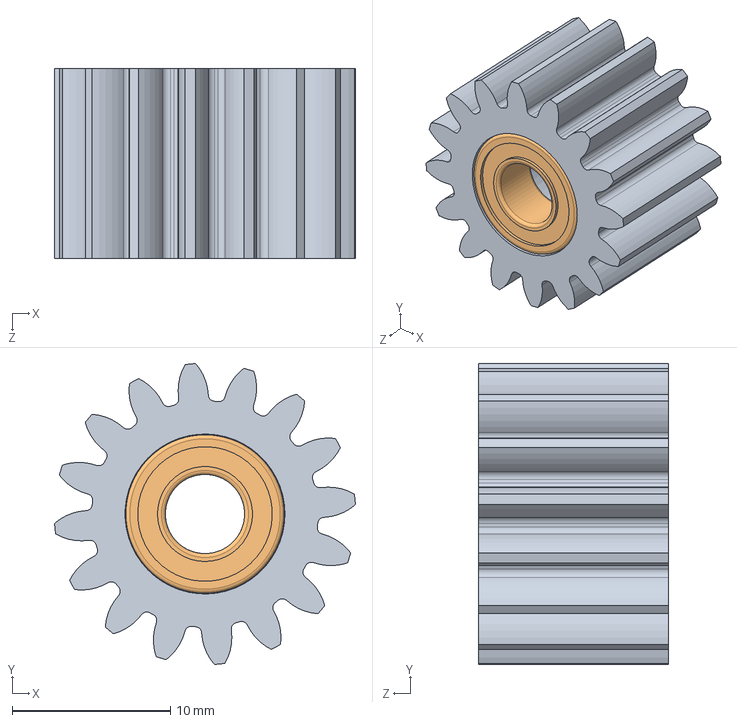
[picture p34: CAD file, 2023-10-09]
Hardware/OpenLeg_V2_Actuator/16T_Planet.SLDASM
19.0 x 19.0 x 12.0 mm
16T_24dp_spur
5mmx10x4_Bearing x 2

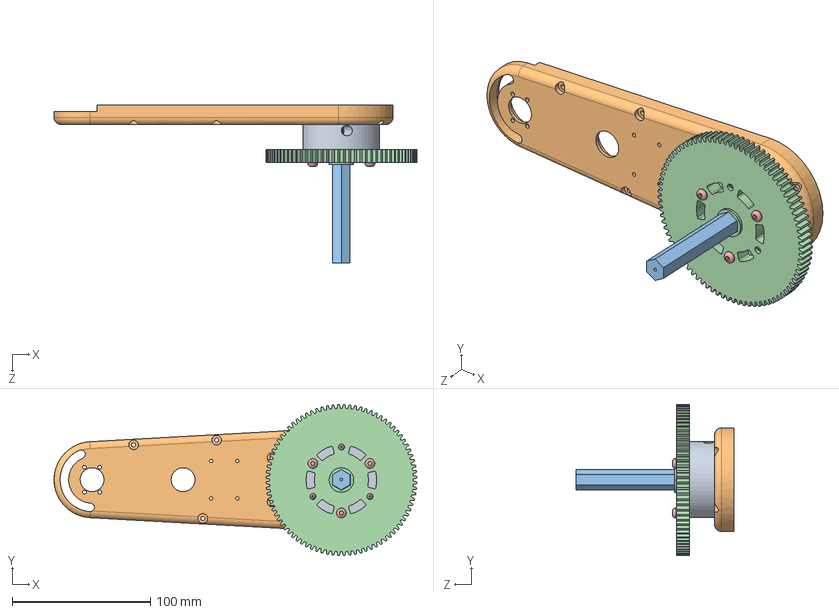
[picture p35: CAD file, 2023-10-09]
Hardware/OpenLeg_Assembly/Leg_Cover_Assembly.SLDASM
262.2 x 109.2 x 114.0 mm
Leg_To_Hip_Adapter
LegCover_EPOWER
Hex_Shaft_Hip
84T_SpurGear
M4_30mm_Screw x 6

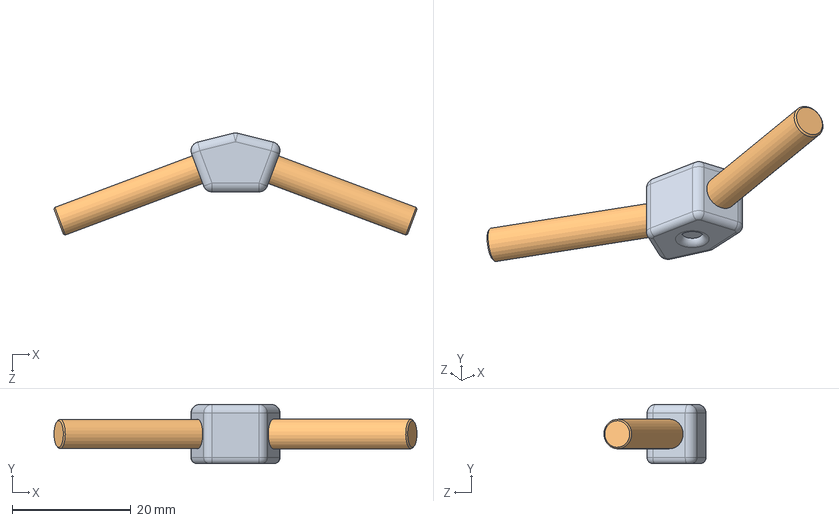
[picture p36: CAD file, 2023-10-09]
Hardware/OpenLeg_Assembly/Idler_Bent_Asm.SLDASM
61.2 x 10.0 x 17.2 mm
IdlerBentConnector
Idler_Shaft_Bent_Half x 2

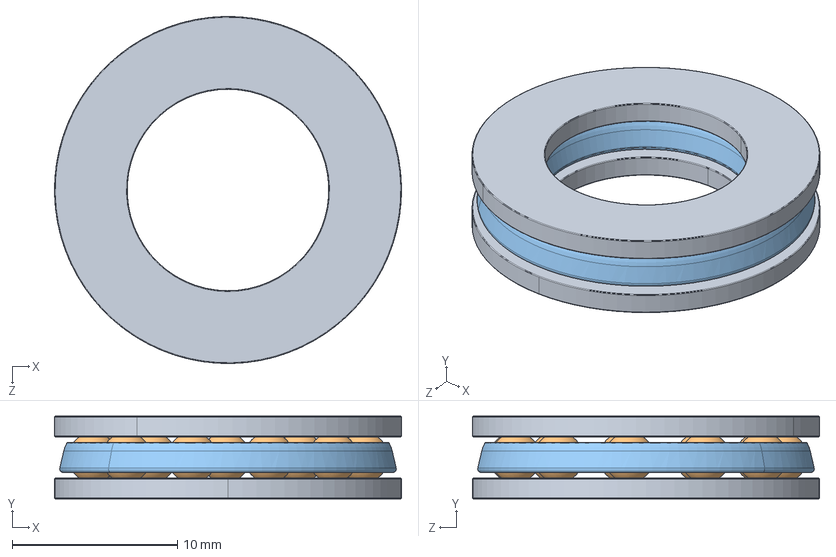
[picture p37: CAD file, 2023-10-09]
Hardware/OpenLeg_V2_Actuator/Thrust_Bearing_12x21x5.SLDASM
21.0 x 5.00 x 21.0 mm
1613-0521-0012 washer.STEP x 2
1613-0521-0012 ball.STEP x 11
1613-0521-0012 carriage.STEP

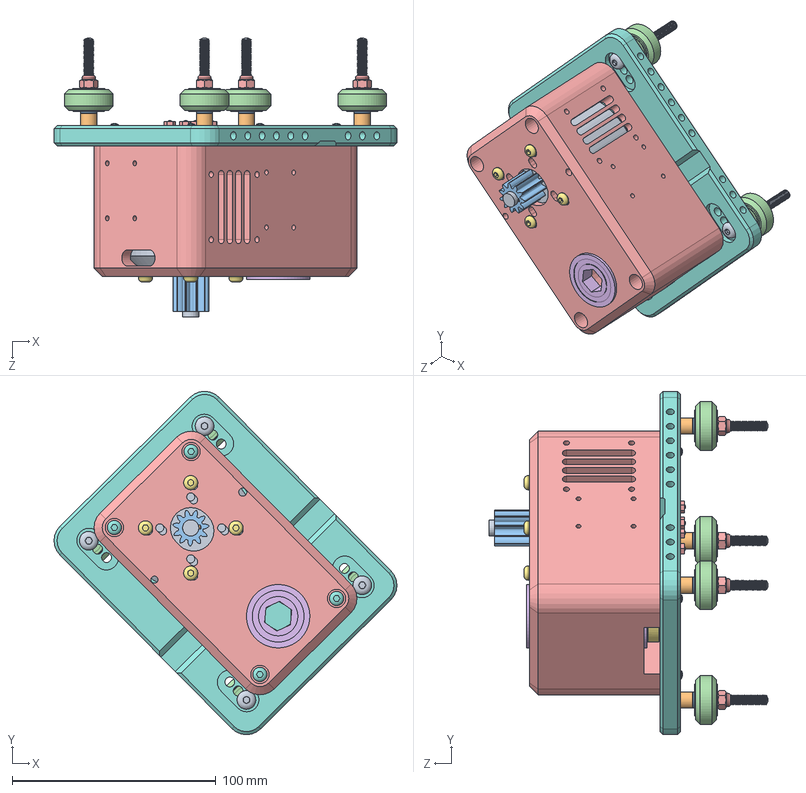
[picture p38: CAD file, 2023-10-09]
Hardware/OpenLeg_Assembly/Hip_Assembly_USER_GUIDE.SLDASM
168.4 x 168.6 x 137.0 mm
EPower60kv
Key_2mm_3mm
11t_pinion
Magnet_for_encoder
MockHip3
HexBearing x 2
M4_8mm_Screw_2 x 4
Gantry2
DIN 557 M4_ DIN 557 M4.stp x 4
AS5047
M2,5_5mm_Standoff x 4
M2,5_Washer x 4
M2,5_Nut x 4
M2.5_x5mm Screw x 4
M4_35mm_Screw x 4
M5x50mm_Screw x 4
M5_6mm_Spacer x 4
M5_1mm_Washer x 4
v-wheel x 4
M5_Locknut x 4

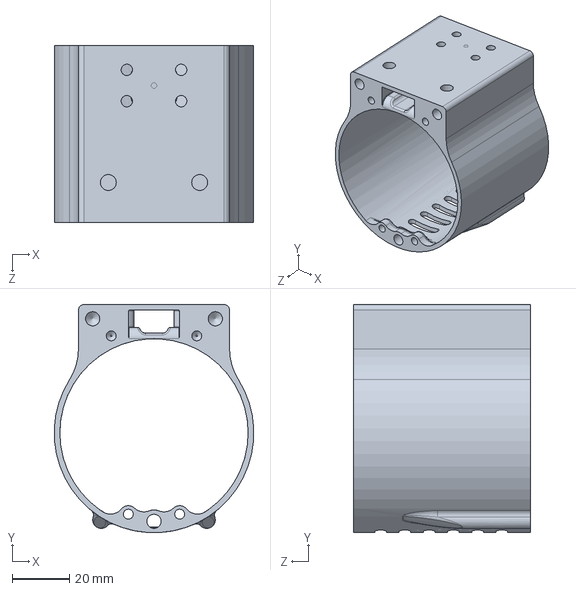
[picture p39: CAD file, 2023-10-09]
Hardware/OpenLeg_V2_Actuator/Mock_Motor_Cover.SLDPRT
69.9 x 79.9 x 62.0 mm

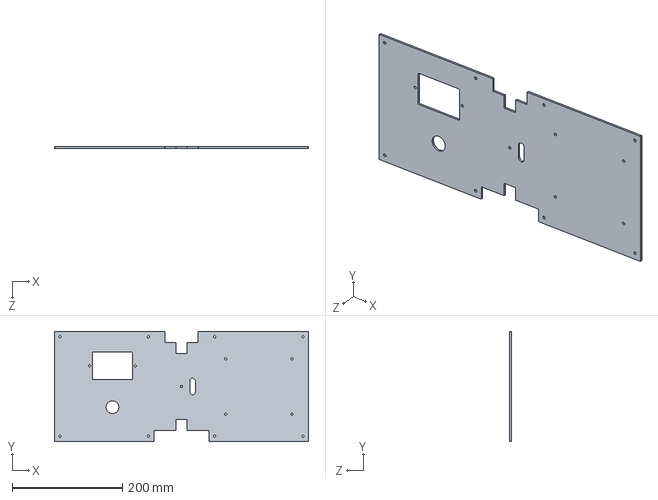
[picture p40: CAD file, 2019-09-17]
Hardware/STEP/Plastic_Test_Stand_Cover.STEP
460.0 x 200.0 x 3.00 mm

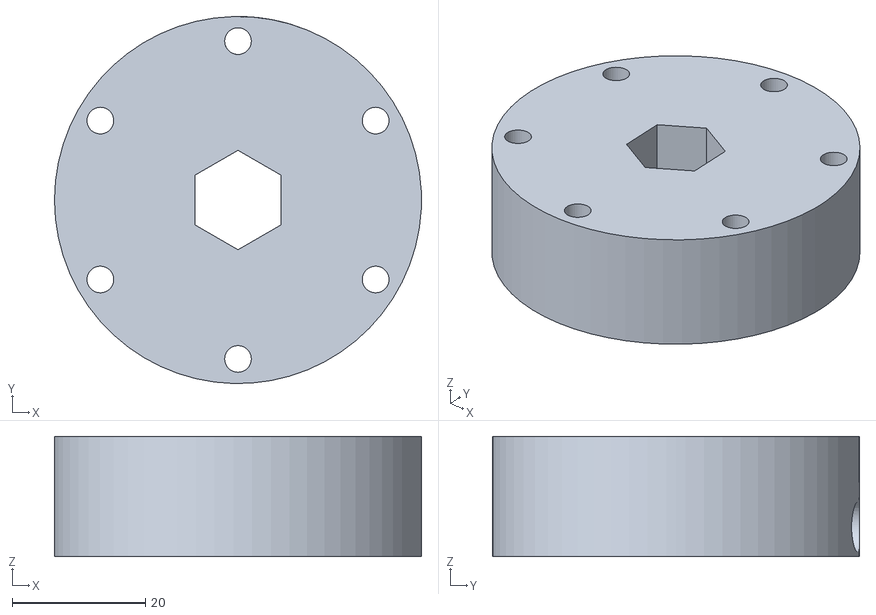
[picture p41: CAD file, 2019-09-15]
Hardware/STL/Leg_To_Hip_Adapter.STL
55.0 x 55.0 x 18.0

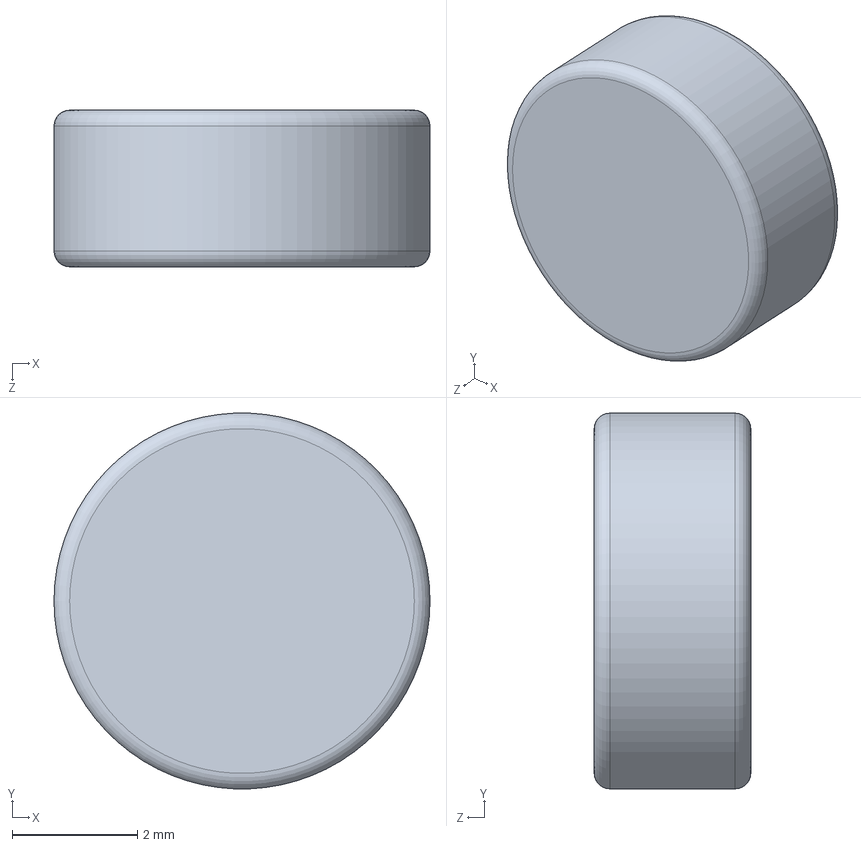
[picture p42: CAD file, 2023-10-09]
Hardware/OpenLeg_V2_Actuator/Magnet_6mm.SLDPRT
6.00 x 5.99 x 2.50 mm

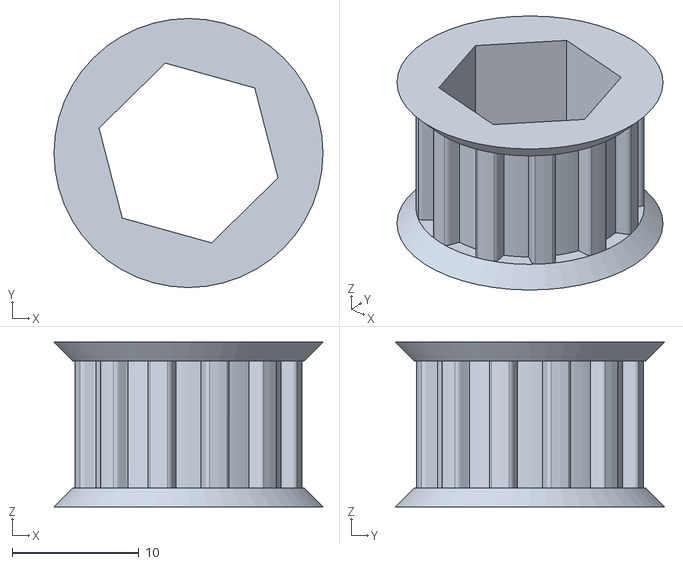
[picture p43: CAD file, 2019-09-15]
Hardware/STL/T5_12T_Pulley.STL
21.2 x 21.2 x 13.0

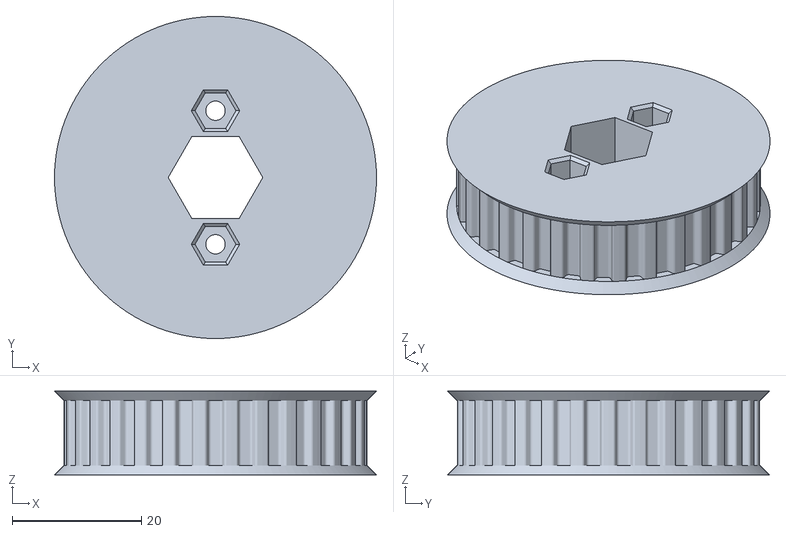
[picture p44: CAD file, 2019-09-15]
Hardware/STL/T5_30T_Pulley.STL
49.9 x 49.9 x 13.0

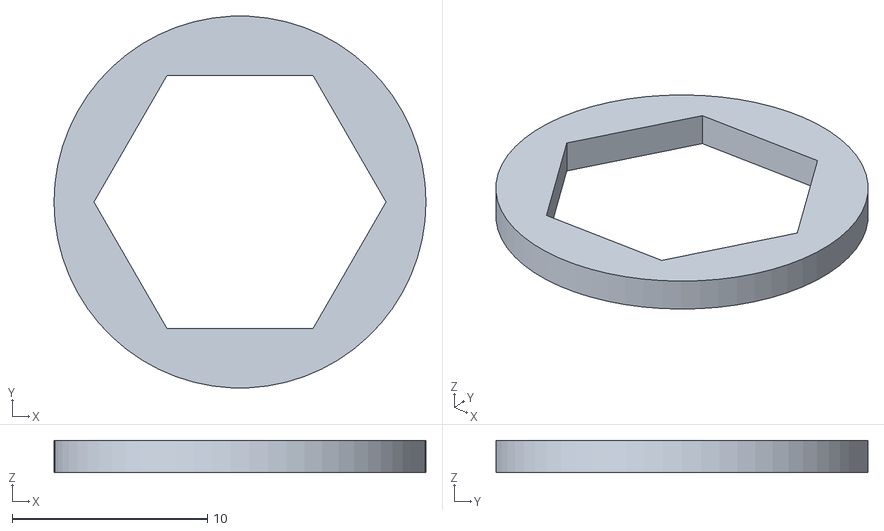
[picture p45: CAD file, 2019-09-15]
Hardware/STL/1,65mm_spacer.STL
19.1 x 19.0 x 1.65

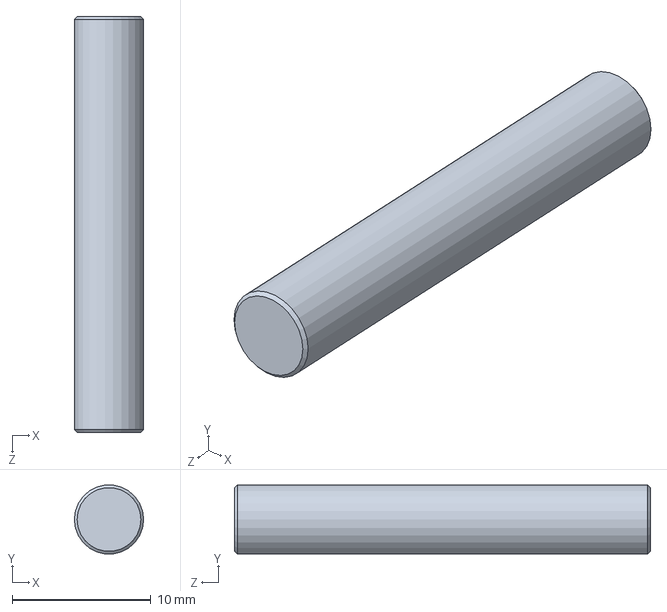
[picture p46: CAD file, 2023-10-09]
Hardware/OpenLeg_Assembly/Hard_Stop_Shaft.SLDPRT
5.00 x 4.96 x 30.0 mm

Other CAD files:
Hardware/OpenLeg_V2_Actuator/1-5_in_Thrust_Bearing_Grainger.SLDASM
Hardware/OpenLeg_V2_Actuator/16T_Carrier_Back_v1.SLDPRT
Hardware/STL/Power_Supply_Holder.STL
Hardware/OpenLeg_V2_Actuator/GearBox_Cap_v2.SLDPRT
Hardware/OpenLeg_Assembly/11t_pinion.SLDPRT
Hardware/OpenLeg_Assembly/84T_SpurGear.SLDPRT
Hardware/OpenLeg_Assembly/AS5047.SLDPRT
Hardware/OpenLeg_Assembly/Curved_foot.SLDPRT
Hardware/OpenLeg_Assembly/EPower60kv.SLDPRT
Hardware/OpenLeg_Assembly/Gantry2.SLDPRT
Hardware/OpenLeg_Assembly/HexBearing.SLDPRT
Hardware/OpenLeg_Assembly/Hex_Shaft_54mm.SLDPRT
Hardware/OpenLeg_Assembly/Hex_Shaft_Hip.SLDPRT
Hardware/OpenLeg_Assembly/IdlerBentConnector.SLDPRT
Hardware/OpenLeg_Assembly/Idler_Shaft_Bent_Half.SLDPRT
Hardware/OpenLeg_Assembly/Key_2mm_3mm.SLDPRT
Hardware/OpenLeg_Assembly/LegCover_EPOWER.SLDPRT
Hardware/OpenLeg_Assembly/LegShell2_EPOWER.SLDPRT
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

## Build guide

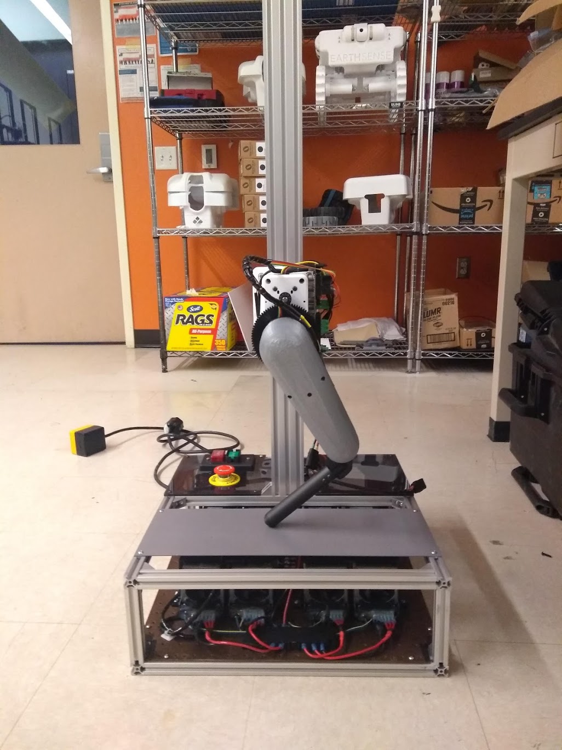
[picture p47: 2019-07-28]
Visuals/4_18_Fully_Working_Assembly.jpg

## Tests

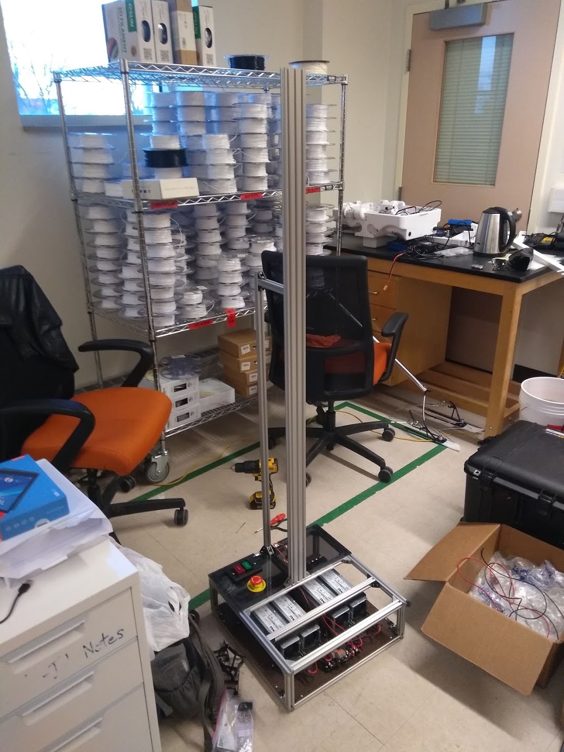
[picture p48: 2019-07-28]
Visuals/Testing_Stand.jpg

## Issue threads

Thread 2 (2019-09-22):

Feedback for future

casainho, 2019-09-22:
Hi.

I don't know where to give feedback so I am opening this issue.

A an user I dream to have a 4 leg walking robot of the medium size dog, that could follow me when I am walking or riding my bicycle. Maybe I am dream to much... Anyway, we need projects like OpenTorque and OpenLeg to make this a reality, so, many thanks for developing and sharing OpenLeg.

I also started the ELegs project, where I want to develop and build for my own an electric legs/exoskeleton with focus on sports for walking and running, just like I do now to go outside and ride my ebike, in future I want to go outside and run and walk using the ELegs: https://github.com/elegs/elegs/wiki

So, many thank you and please keep developing OpenLeg. We know that 3D printing is very accessible now, as also electronics and tools and libraries to develop the software, so, should be possible to develop and build our own walking robots as RepRap community did for 3D printers, Arduino, etc!!

JoeyByrnes, 2019-09-23:
Thanks for the feedback. I am absolutely continuing to develop this project, this is just the start.

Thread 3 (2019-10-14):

URDF model does not exist

muratKeys, 2019-10-14:
Hi,
When I run the Leg_Stand_Sim.py file, I get the following error:

`b3Printf:` URDF file 'First_App_Test_Stand_urdf4.SLDASM.urdf' not found.
`
And I could not find the URDF file in the repository.
Where can I find?

JoeyByrnes, 2019-10-14:
Hi,
Thanks for bringing that to my attention, I made that URDF before building the leg so it was just an initial concept design, I'll make a new one more accurate to the real leg and post that when it's ready. Probably with an updated python script too.

As you use the project keep in mind that OpenLeg isn't a finished product, it's still very much under development. You can expect everything in the assembly guide to be ready to use but for things not listed in the guide you should expect that there is still development to do.

Best,
Joey

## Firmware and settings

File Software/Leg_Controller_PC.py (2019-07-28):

##################################################
## OpenLeg Python Controller using OdriveTool
##
## Authors: Joseph Byrnes & Kanyon Edvall
##################################################

import odrive
import time
import sys
import math
import matplotlib.pyplot as plt
import numpy as np
import pandas as pd



cur_x = 0
cur_y = 360

safe_mode = True
linear = False
fast = False
slow = False
record = False
xpos = 0
ypos = -200

start_time = 0

setx = open("x_set.txt","w+")
sety = open("y_set.txt","w+")
kr = open("knee_reading.txt","w+")
ks = open("knee_setpoint.txt","w+")
hr = open("hip_reading.txt","w+")
hs = open("hip_setpoint.txt","w+")
tm = open("time.txt","w+")
crk = open("currentk.txt","w+")
crh = open("currenth.txt","w+")

def moveJoint(dest_x, dest_y):
	xpos = dest_x
	ypos = dest_y
	q2 = -math.acos((xpos*xpos + ypos*ypos - a1*a1 - a2*a2)/(2*a1*a2))
	q1 = math.atan2(ypos, xpos) + math.atan2(a2*math.sin(q2), a1 + a2*math.cos(q2)) - q2

	#print("Generated q2: " + str(q2) + ", q1: " + str(q1))

	knee_set = q2*rad_to_cpr*knee_ratio + zero_pos_knee
	hip_set = -q1*rad_to_cpr*hip_ratio + zero_pos_hip

	knee_pos = od.axis0.encoder.pos_estimate
	hip_pos = od.axis1.encoder.pos_estimate

	time_read = time.time() - start_time
	if record:
		kr.write("%f\r\n" % knee_pos)
		hr.write("%f\r\n" % hip_pos)
		ks.write("%f\r\n" % knee_set)
		hs.write("%f\r\n" % hip_set)
		tm.write("%f\r\n" % time_read)
		setx.write("%f\r\n" % dest_x)
		sety.write("%f\r\n" % dest_y)

		currentk = math.fabs(od.axis0.motor.current_meas_phC) + math.fabs(od.axis0.motor.current_meas_phB)
		crk.write("%f\r\n" % currentk)

		currenth = math.fabs(od.axis1.motor.current_meas_phC) + math.fabs(od.axis1.motor.current_meas_phB)
		crh.write("%f\r\n" % currenth)


	# if fast:
	knee.pos_setpoint = int(knee_set)
	hip.pos_setpoint = int(hip_set)
	# else:
	# 	knee.move_to_pos(int(knee_set))
	# 	hip.move_to_pos(int(hip_set))

def moveLinear(dest_x, dest_y):
	global cur_x
	global cur_y
	resolution = 10
	dist = ((dest_x - cur_x)**2 + (dest_y - cur_y) ** 2)**0.5

	dist_y = math.fabs(cur_y - dest_y)
	dist_x = math.fabs(cur_x - dest_x)

	num_points = dist/resolution
	dx = math.copysign(dist_x/num_points, dest_x-cur_x)
	dy = math.copysign(dist_y/num_points, dest_y-cur_y)

	for i in range(int(num_points)):
		moveJoint(cur_x+dx, cur_y+dy)
		cur_x = cur_x+dx
		cur_y = cur_y+dy
		# time.sleep(0.0000001)


def moveLinearSlow(dest_x, dest_y):
	global cur_x
	global cur_y
	resolution = 0.1
	dist = ((dest_x - cur_x)**2 + (dest_y - cur_y) ** 2)**0.5

	dist_y = math.fabs(cur_y - dest_y)
	dist_x = math.fabs(cur_x - dest_x)

	num_points = dist/resolution
	dx = math.copysign(dist_x/num_points, dest_x-cur_x)
	dy = math.copysign(dist_y/num_points, dest_y-cur_y)

	for i in range(int(num_points)):
		moveJoint(cur_x+dx, cur_y+dy)
		cur_x = cur_x+dx
		cur_y = cur_y+dy
		# time.sleep(0.0000001)


def moveLinearadj(dest_x, dest_y, res):
	global cur_x
	global cur_y
	resolution = res
	dist = ((dest_x - cur_x)**2 + (dest_y - cur_y) ** 2)**0.5

	dist_y = math.fabs(cur_y - dest_y)
	dist_x = math.fabs(cur_x - dest_x)

	num_points = dist/resolution
	dx = math.copysign(dist_x/num_points, dest_x-cur_x)
	dy = math.copysign(dist_y/num_points, dest_y-cur_y)

	for i in range(int(num_points)):
		moveJoint(cur_x+dx, cur_y+dy)
		cur_x = cur_x+dx
		cur_y = cur_y+dy
		# time.sleep(0.0000001)


# walk_x = [-0.0116,-0.011,-0.0104,-0.0098,-0.0092,-0.0086,-0.008,-0.0074,-0.0068,-0.0062,-0.0056,-0.005,-0.0044,-0.0038,-0.0032,-0.0026,-0.002,-0.0014,-0.0008,-0.0002,0.0004,0.001,0.0016,0.0022,0.0028,0.0034,0.004,0.0046,0.0052,0.0058,0.0064,0.007,0.0076,0.0082,0.0088,0.0094,0.01,0.0106,0.0112,0.0118,0.0122,0.0116,0.011,0.0104,0.0098,0.0092,0.0086,0.008,0.0074,0.0068,0.0062,0.0056,0.005,0.0044,0.0038,0.0032,0.0026,0.002,0.0014,0.0008,0.0002,-0.0004,-0.001,-0.0016,-0.0022,-0.0028,-0.0034,-0.004,-0.0046,-0.0052,-0.0058,-0.0064,-0.007,-0.0076,-0.0082,-0.0088,-0.0094,-0.01,-0.0106,-0.0112,-0.0118,-0.0124]
# print(len(walk_x))
# walk_y = [-0.022388,-0.024077,-0.025346,-0.026247,-0.026834,-0.027153,-0.02725,-0.027167,-0.026942,-0.026612,-0.02621,-0.025765,-0.025304,-0.024851,-0.024428,-0.02405,-0.023734,-0.023491,-0.02333,-0.023255,-0.02327,-0.023374,-0.023564,-0.023832,-0.02417,-0.024564,-0.025,-0.025458,-0.025916,-0.02635,-0.026732,-0.02703,-0.027212,-0.02724,-0.027074,-0.02667,-0.025984,-0.024966,-0.023564,-0.021722,-0.018,-0.014189,-0.012678,-0.011566,-0.010668,-0.009913,-0.0092639,-0.0086984,-0.008202,-0.0077648,-0.0073793,-0.0070401,-0.006743,-0.0064848,-0.0062629,-0.0060752,-0.0059203,-0.0057967,-0.0057037,-0.0056404,-0.0056065,-0.0056016,-0.0056258,-0.0056793,-0.0057624,-0.0058756,-0.00602,-0.0061966,-0.0064069,-0.0066528,-0.0069365,-0.0072613,-0.0076308,-0.0080501,-0.0085258,-0.0090669,-0.0096862,-0.010403,-0.011247,-0.012276,-0.013618,-0.015782]

walk_y_2 = [-0.022701,-0.024316,-0.02552,-0.026366,-0.026904,-0.027184,-0.027248,-0.027138,-0.026893,-0.026549,-0.026138,-0.025688,-0.025227,-0.024778,-0.024361,-0.023993,-0.023689,-0.023458,-0.023311,-0.023251,-0.023281,-0.0234,-0.023603,-0.023884,-0.024232,-0.024635,-0.025075,-0.025535,-0.025991,-0.026418,-0.026788,-0.02707,-0.027228,-0.027227,-0.027024,-0.026577,-0.025839,-0.024761,-0.023289,-0.023,-0.019334,-0.017885,-0.016823,-0.015969,-0.015254,-0.014643,-0.014114,-0.013653,-0.013251,-0.0129,-0.012596,-0.012334,-0.012111,-0.011926,-0.011775,-0.011658,-0.011574,-0.011521,-0.0115,-0.011511,-0.011553,-0.011626,-0.011732,-0.011872,-0.012046,-0.012256,-0.012504,-0.012794,-0.013129,-0.013513,-0.013953,-0.014458,-0.01504,-0.015717,-0.016519,-0.017501,-0.018786,-0.020865]
walk_x_2 = [0.0113,-0.0109,-0.0103,-0.0097,-0.0091,-0.0085,-0.0079,-0.0073,-0.0067,-0.0061,-0.0055,-0.0049,-0.0043,-0.0037,-0.0031,-0.0025,-0.0019,-0.0013,-0.0007,-0.0001,0.0005,0.0011,0.0017,0.0023,0.0029,0.0035,0.0041,0.0047,0.0053,0.0059,0.0065,0.0071,0.0077,0.0083,0.0089,0.0095,0.0101,0.0107,0.0113,0.0113,0.0107,0.0101,0.0095,0.0089,0.0083,0.0077,0.0071,0.0065,0.0059,0.0053,0.0047,0.0041,0.0035,0.0029,0.0023,0.0017,0.0011,0.0005,-0.0001,-0.0007,-0.0013,-0.0019,-0.0025,-0.0031,-0.0037,-0.0043,-0.0049,-0.0055,-0.0061,-0.0067,-0.0073,-0.0079,-0.0085,-0.0091,-0.0097,-0.0103,-0.0109,-0.0115]
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

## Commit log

2019-07-28 Added Main Leg STLs
    [84T_SpurGear.STL, Gantry2.STL, Hip.STL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]
2019-07-28 Added Power Supply Holder
    [Power_Supply_Holder.STL]
2019-07-28 Added PC Leg Controller used for ECE445 Demo
2019-09-12 Added Pulley STLs
    [T5-30T_Pulley.STL, T5_12T_Pulley.STL]
2019-09-12 Changed T5 12T Pulley name
    [T5_30T_Pulley.STL]
2019-09-15 Added STL Files
    [1,65mm_spacer.STL, Gantry.STL, IdlerBentConnector.STL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]
2019-09-15 Added let_to_hip_adapter
    [Leg_To_Hip_Adapter.STL]
2019-09-17 Added Assembly Guide
    [Plastic_Test_Stand_Cover.STEP]
2019-09-19 Added ODrive Wiring Guide
2019-09-24 Added Power Supply Wiring Guide
2023-10-09 Added SolidWorks Source Files
    [1-5_in_Thrust_Bearing_Grainger.SLDASM, 11t_pinion.SLDPRT, 16T_24dp_spur.sldprt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]
